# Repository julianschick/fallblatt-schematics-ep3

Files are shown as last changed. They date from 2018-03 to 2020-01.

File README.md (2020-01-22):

# Fallblattanzeiger der Deutschen Bahn

Die Deutsche Bahn verwendete lange Zeit standardisierte Fallblattanzeigemodule mit Platinen, die mit *MANTronic* beschriftet sind, also vermutlich von der Firma MAN hergestellt wurden.

Möchte man diese alten Module wieder zum klappern bringen, so hat man grundsätzlich erstmal zwei Möglichkeiten. Die Module wurden offenbar über eine RS485-Schnittstelle angesteuert. Das Protokoll ist vermutlich ein Protokoll ähnlich dem CAN-Bus. Meine gründliche Recherche ergab allerdings keine Quellen im Internet, denen bekannt ist, wie dieses Protokoll genau aussieht. Diese Möglichkeit ist daher eher schwierig.

Eine andere Möglichkeit besteht darin, den zentralen ZiLOG-Microcontroller auf der Platine durch einen eigenen Microcontroller zu ersetzen. Ich habe zu diesem Zweck den ZiLOG-Chip von der Platine geschnitten. Praktischerweise sind auf der Platine nicht nur die SMD-Lötpads für den ZiLOG-Chip, sondern auch etwas größere Pads im DIP-Raster, an die man sehr gut Kabel anlöten kann. Vermutlich ein überbleibsel von älteren Platinenversionen, bei denen ein größerer Microcontroller verwendet wurde.

Mit einer Kombination aus eigener Intuition und Bestätigung durch die Schaltpläne dieses [Hackaday-Projekts](https://hackaday.io/project/9070-fallblattfahrzielanzeige-of-s-bahn-berlin) war es nicht schwer, die Pinbelegung des ZiLOG-Controllers zu ermitteln und so herauszufinden, welche Pins angesteuert bzw. ausgelesen werden müssen. Weiter unten habe ich das mit einer Skizze und einem Foto dokumentiert.

Gemäß der Einteilung im [Wikipedia-Artikel](https://de.wikipedia.org/wiki/Fallblattanzeige) in die vom Aufbau her zu unterscheidenden Epochen 1 bis 4 fällt diese Anzeige in die Epoche 3.

## Funktionsweise

Die Funktionsweise des Fallblattmoduls ist gar nicht so kompliziert. Die Blätter sitzen auf einer Welle die über ein Getriebe von einem Synchronmotor (Berger Lahr RSM 42/12 NG) angetrieben wird, der tatsächlich auch heute noch erhältlich ist ([Datenblatt](https://www.abi.nl/assets/uploads/Downloads/Aandrijvingen/Kleine%20vertragingsmotoren/Synchroonmotoren/Catalogus_RSM_D.pdf)).
Damit der Motor weiß, wann er anhalten soll, sind zwei Infrarot-Transmitter mit Photodioden als Sensoren verbaut. Ein Sensor erzeugt pro fallendem Blatt einen erhöhten Spannungspegel, der andere dient zur Erkennung der Nullposition und weist nur einmal pro Umdrehung der ganzen Welle einen erhöhten Spannungspegel auf. Das ganze wird durch weiße Blenden bewerkstelligt, die beim Vorbeistreichen am Sensor durch die Reflektion der Infrarotstrahlen des Transmitters für mehr Einfall von Infrarotstrahlung in die Photodiode und dadurch einen höheren Spannungspegel sorgen.

Die Verdrahtung der Sensoren auf der Platine ist etwas eigenwillig. Beide Sensoren gehen auf den gleichen Eingang (Sensor IN), an dem mit Hilfe eines ADC die anliegende Spannung messen kann. Um die Sensoren einzeln abfragen zu können, kann man die Sensoren getrennt mit Spannung versorgen (Sensor 1 / Sensor 2) und dann jeweils nur den Sensor auslesen, der mit Spannung versorgt wird. Der Motor ist einfach anzusteuern: Zieht man den Motor-Pin auf LOW, läuft der Motor los, zieht man ihn auf HIGH (3,3V oder 5V), bleibt der Motor stehen.

## Pinbelegung ZiLOG
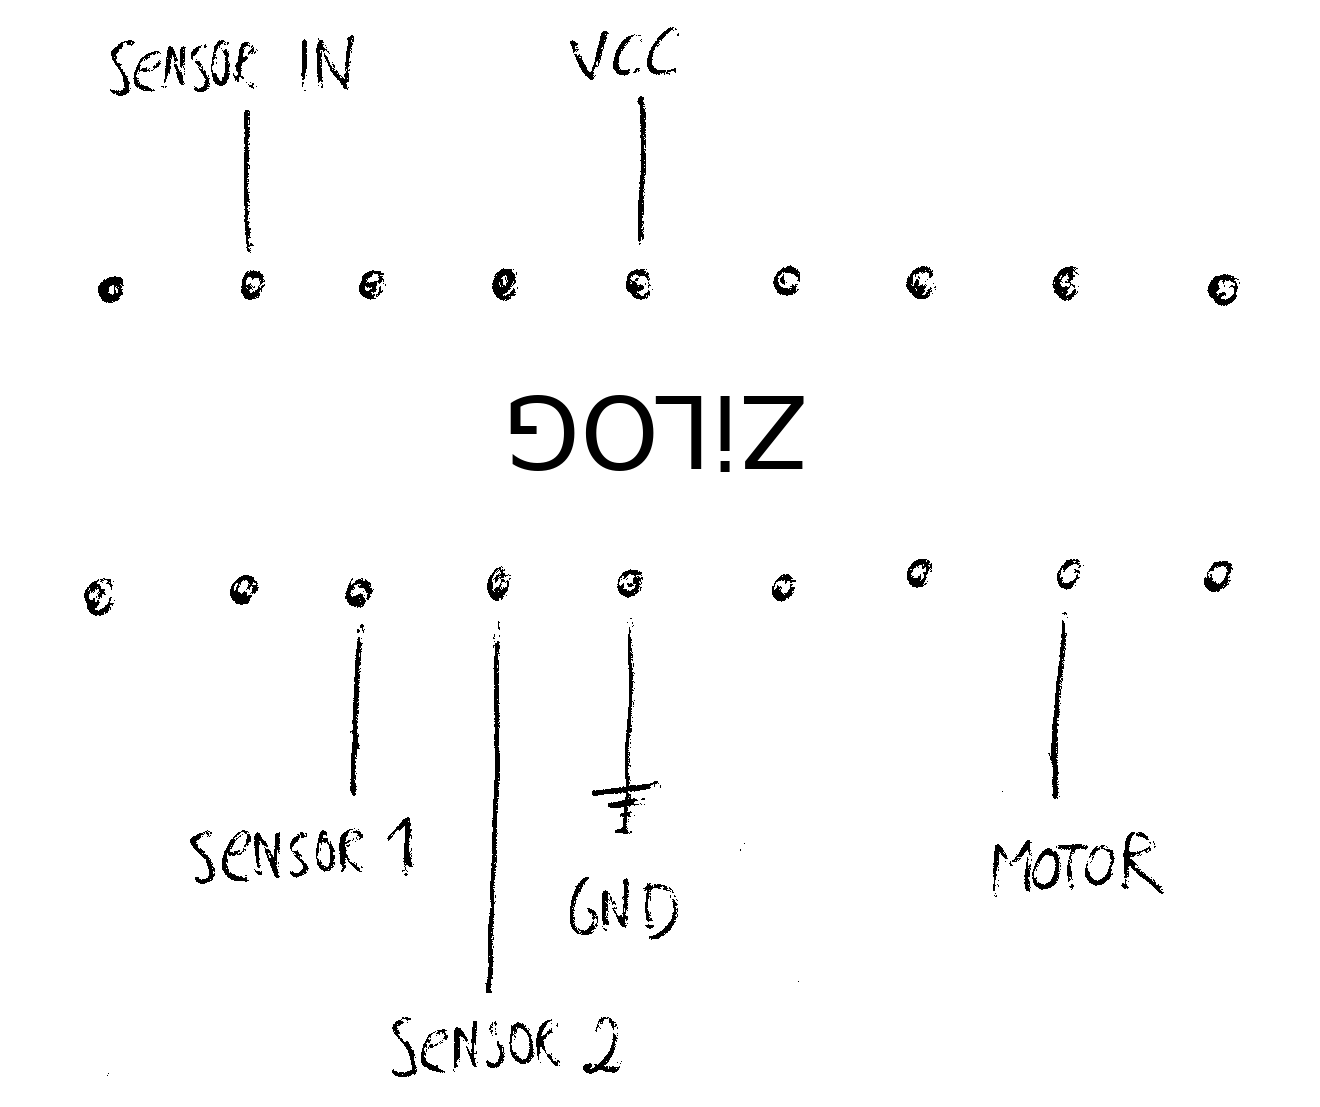
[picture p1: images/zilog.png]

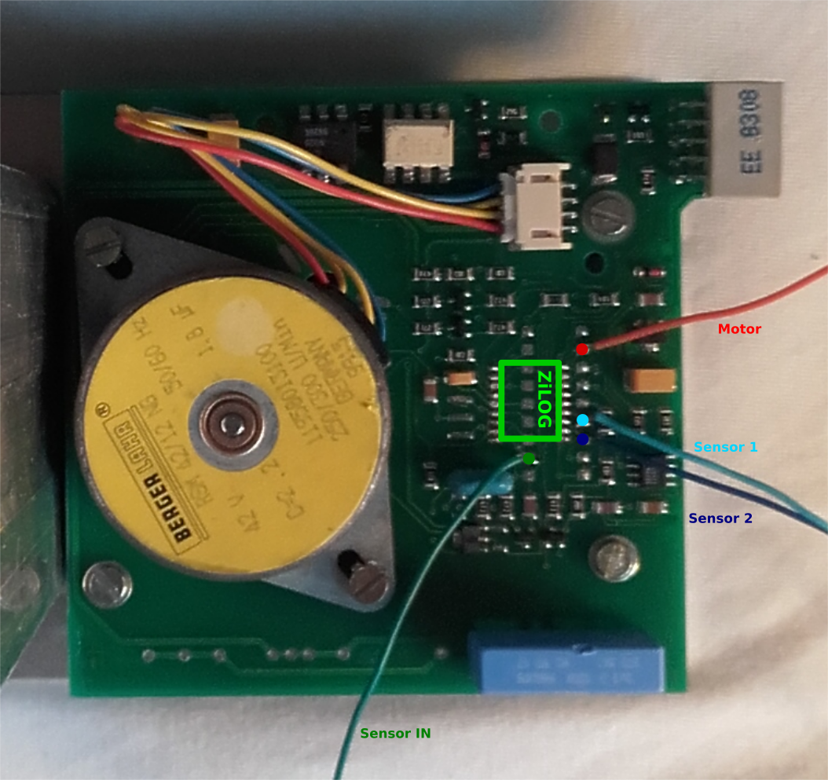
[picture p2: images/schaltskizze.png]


## Stromversorgung

Die Platine hat zwei Stromkreise, ein Niederspannungsstromkreis für die Steuerungselektronik, der ursprünglich wohl mit 5 V DC betrieben wurde. Ich habe auch mit nur 3.3 V DC keine Probleme festgestellt. Der andere Stromkreis sollte mit etwa 42 V AC bei 50 Hz gespeist werden. Mit diesem Strom wird der Synchronmotor zum Antrieb der Welle betrieben. Die folgende Skizze zeigt die Pinbelegung des Wannensteckers am Rand der Platine bezüglich der Spannungsversorgung.

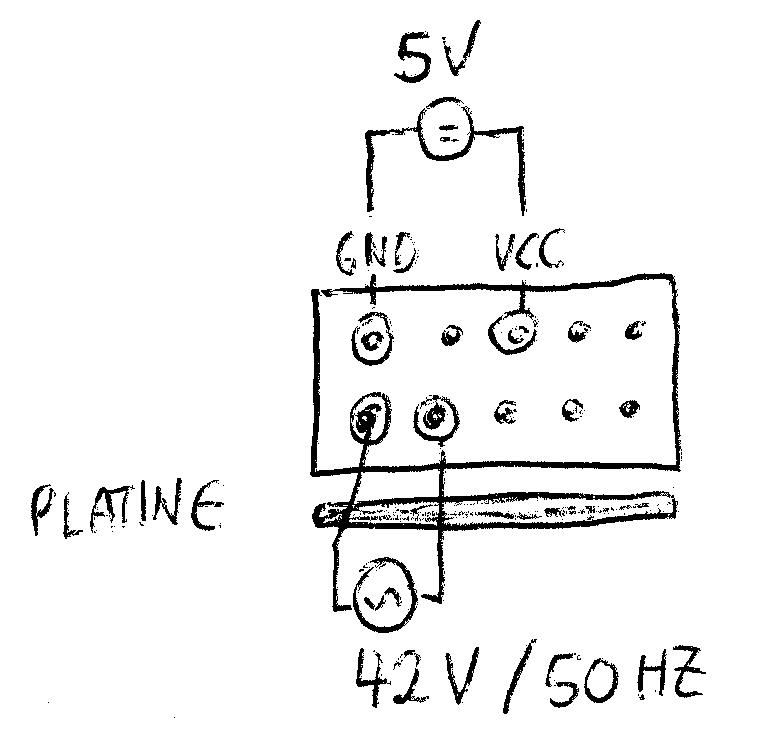
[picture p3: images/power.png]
Stromversorgung


## Code

Code für die Platine kann in den Repositories [fallblatt-code-legacy](https://github.com/julianschick/fallblatt-code-legacy) und [fallblatt-code](https://github.com/julianschick/fallblatt-code) gefunden werden, wobei letzterer aktueller und mit mehr Funktionen ausgestattet ist.

## Teileliste

Mit passenden Artikelbezeichnungen für den Berliner Elektroteilehändler [Segor](https://www.segor.de).

Anzahl | Beschreibung | Segor-Artikelbezeichnung | Alt. Link
--|--|--|--
1 | Schraubklemme 2-polig RM 7,5mm | *ARK 2-Lift/RM7,5*
1 | Varistor >300V RM 7,5mm | *VDR 300-K 7* | [Reichelt](https://www.reichelt.de/varistor-rm-7-5-mm-300-v-10-epc-b72210-s030-p239932.html)
1 | Brückengleichrichter Rund, Wechselstrompins gegenüber, RM 5mm | *B 80C1500 R* | [Reichelt](https://www.reichelt.de/brueckengleichrichter-100-v-1-5-a-b70c1500rund-p181713.html)
1 | Transformator 9V _Block VB 2,0/1/9_ | | [Reichelt](https://www.reichelt.de/printtrafo-2-va-9-v-222-ma-rm-20-mm-ei-30-15-5-109-p27328.html)
1 | Transformator 2x24V *Block VC 10/2/24* | | [Reichelt](https://www.reichelt.de/printtrafo-10-va-2x-24-v-2x-208-ma-rm-27-5-mm-ei-48-16-8-224-p27492.html)
1 | ESP32-Development-Board (es gibt 2 Varianten bei eBay, für diese Platine wird die unüblichere mit 19 Pins je Reihe und GND/VCC auf gegenüberliegenden, nicht nebeneinanderliegenden Pins benötigt; diese wird oft unter dem Namen _ESP32S_ verkauft.) |
1 | Spannungsregler 3,3V Formfaktor TO-220 _STM LD1117 V33C_ | *LD 1117 V33* | [Reichelt](https://www.reichelt.de/ldo-regler-fest-3-3-v-to-220-ld1117-v33c-p200891.html)
1 | Elektrolytkondensator 470u, >12V, RM 5mm | *ELRA 470u-25/105°lowESR* |
1 | Elektrolytkondensator 10u, >12V, RM 2mm | *ELRA 470u-35/105°* |
1 | Kondensator 100n, >12V, RM 2,5mm | *u10-R2.5-X7R* |
1 | D-Sub Buchse 9-polig, Printmontage 90°, Abstand Pinreihe zu Steckerfläche 10mm | DS09F-90°-10mm |
1 | D-Sub Buchse 25-polig, Printmontage 90°, Abstand Pinreihe zu Steckerfläche 10mm | DS25F-90°-10mm |
4 | Pinheader 20-polig, Female, Vertikal, RM 2,54mm | 
2 | Pinheader 2-polig, Male, Vertikal, RM 2,54mm

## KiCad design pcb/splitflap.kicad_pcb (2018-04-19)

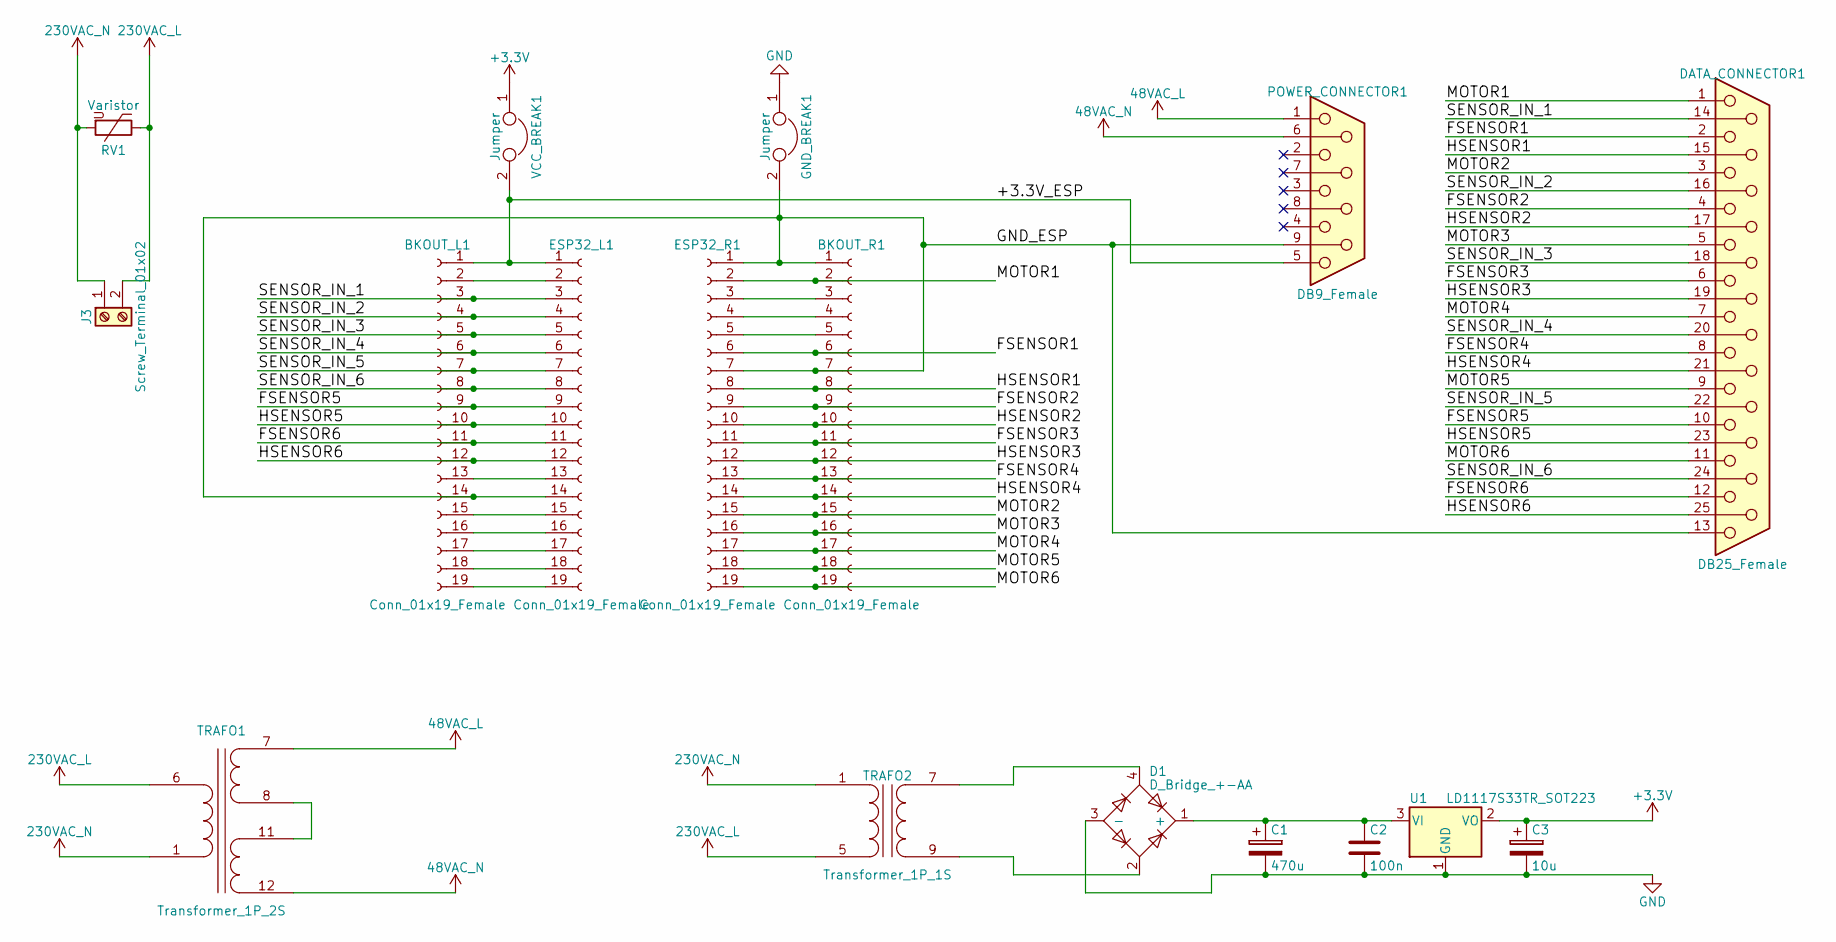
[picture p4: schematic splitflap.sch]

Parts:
BKOUT_L1: Conn_01x19_Female; Socket_Strip_Straight_1x20_Pitch2.54mm
BKOUT_R1: Conn_01x19_Female; Socket_Strip_Straight_1x20_Pitch2.54mm
C1: 470u; CP_Radial_D8.0mm_P5.00mm
C2: 100n; C_Rect_L4.0mm_W2.5mm_P2.50mm
C3: 10u; CP_Radial_D4.0mm_P2.00mm
D1: D_Bridge_+-AA; Diode_Bridge_Round_D8.9mm
DATA_CONNECTOR1: DB25_Female; DSUB-25_Female_Horizontal_Pitch2.77x2.54mm_EdgePinOffset9.4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
ESP32_L1, ESP32_R1: Conn_01x19_Female; Socket_Strip_Straight_1x20_Pitch2.54mm
GND_BREAK1: Jumper; Pin_Header_Straight_1x02_Pitch2.54mm
J3: Screw_Terminal_01x02; TerminalBlock_MetzConnect_Type171_RT13702HBWC_Pitch7.50mm
POWER_CONNECTOR1: DB9_Female; DSUB-9_Female_Horizontal_Pitch2.77x2.54mm_EdgePinOffset9.40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
RV1: Varistor; RV_Disc_D12_W3.9_P7.5
TRAFO1: Transformer_1P_2S; Transformer_CHK_EI48-10VA_2xSec_BLOCK
TRAFO2: Transformer_1P_1S; Transformer_CHK_EI30-2VA_1xSec
U1: LD1117S33TR_SOT223; TO-220-3_Vertical
VCC_BREAK1: Jumper; Pin_Header_Straight_1x02_Pitch2.54mm

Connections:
48VAC_L: POWER_CONNECTOR1.1, TRAFO1.7 (SA)
48VAC_N: POWER_CONNECTOR1.6, TRAFO1.12 (SD)
230VAC_L: J3.2, RV1.1, TRAFO1.6 (AA), TRAFO2.5 (AB)
230VAC_N: J3.1, RV1.2, TRAFO1.1 (AB), TRAFO2.1 (AA)
+3V3: C3.1, U1.2 (VO), VCC_BREAK1.1
/+3.3V_ESP: BKOUT_L1.1, ESP32_L1.1, POWER_CONNECTOR1.5, VCC_BREAK1.2
/FSENSOR1: BKOUT_R1.6, DATA_CONNECTOR1.2, ESP32_R1.6
/FSENSOR2: BKOUT_R1.9, DATA_CONNECTOR1.4, ESP32_R1.9
/FSENSOR3: BKOUT_R1.11, DATA_CONNECTOR1.6, ESP32_R1.11
/FSENSOR4: BKOUT_R1.13, DATA_CONNECTOR1.8, ESP32_R1.13
/FSENSOR5: BKOUT_L1.9, DATA_CONNECTOR1.10, ESP32_L1.9
/FSENSOR6: BKOUT_L1.11, DATA_CONNECTOR1.12, ESP32_L1.11
/GND_ESP: BKOUT_L1.14, BKOUT_R1.1, BKOUT_R1.7, DATA_CONNECTOR1.13, ESP32_L1.14, ESP32_R1.1, ESP32_R1.7, GND_BREAK1.2, POWER_CONNECTOR1.9
/HSENSOR1: BKOUT_R1.8, DATA_CONNECTOR1.15, ESP32_R1.8
/HSENSOR2: BKOUT_R1.10, DATA_CONNECTOR1.17, ESP32_R1.10
/HSENSOR3: BKOUT_R1.12, DATA_CONNECTOR1.19, ESP32_R1.12
/HSENSOR4: BKOUT_R1.14, DATA_CONNECTOR1.21, ESP32_R1.14
/HSENSOR5: BKOUT_L1.10, DATA_CONNECTOR1.23, ESP32_L1.10
/HSENSOR6: BKOUT_L1.12, DATA_CONNECTOR1.25, ESP32_L1.12
/MOTOR1: BKOUT_R1.2, DATA_CONNECTOR1.1, ESP32_R1.2
/MOTOR2: BKOUT_R1.15, DATA_CONNECTOR1.3, ESP32_R1.15
/MOTOR3: BKOUT_R1.16, DATA_CONNECTOR1.5, ESP32_R1.16
/MOTOR4: BKOUT_R1.17, DATA_CONNECTOR1.7, ESP32_R1.17
/MOTOR5: BKOUT_R1.18, DATA_CONNECTOR1.9, ESP32_R1.18
/MOTOR6: BKOUT_R1.19, DATA_CONNECTOR1.11, ESP32_R1.19
/SENSOR_IN_1: BKOUT_L1.3, DATA_CONNECTOR1.14, ESP32_L1.3
/SENSOR_IN_2: BKOUT_L1.4, DATA_CONNECTOR1.16, ESP32_L1.4
/SENSOR_IN_3: BKOUT_L1.5, DATA_CONNECTOR1.18, ESP32_L1.5
/SENSOR_IN_4: BKOUT_L1.6, DATA_CONNECTOR1.20, ESP32_L1.6
/SENSOR_IN_5: BKOUT_L1.7, DATA_CONNECTOR1.22, ESP32_L1.7
/SENSOR_IN_6: BKOUT_L1.8, DATA_CONNECTOR1.24, ESP32_L1.8
GND: C1.2, C2.2, C3.2, D1.3 (-), GND_BREAK1.1, U1.1 (GND)
unnamed: BKOUT_L1.2, ESP32_L1.2
unnamed: BKOUT_L1.13, ESP32_L1.13
unnamed: BKOUT_L1.15, ESP32_L1.15
unnamed: BKOUT_L1.16, ESP32_L1.16
unnamed: BKOUT_L1.17, ESP32_L1.17
unnamed: BKOUT_L1.18, ESP32_L1.18
unnamed: BKOUT_L1.19, ESP32_L1.19
unnamed: BKOUT_R1.3, ESP32_R1.3
unnamed: BKOUT_R1.4, ESP32_R1.4
unnamed: BKOUT_R1.5, ESP32_R1.5
unnamed: C1.1, C2.1, D1.1 (+), U1.3 (VI)
unnamed: D1.2, TRAFO2.9 (SA)
unnamed: D1.4, TRAFO2.7 (SB)
unnamed: TRAFO1.8 (SB), TRAFO1.11 (SC)

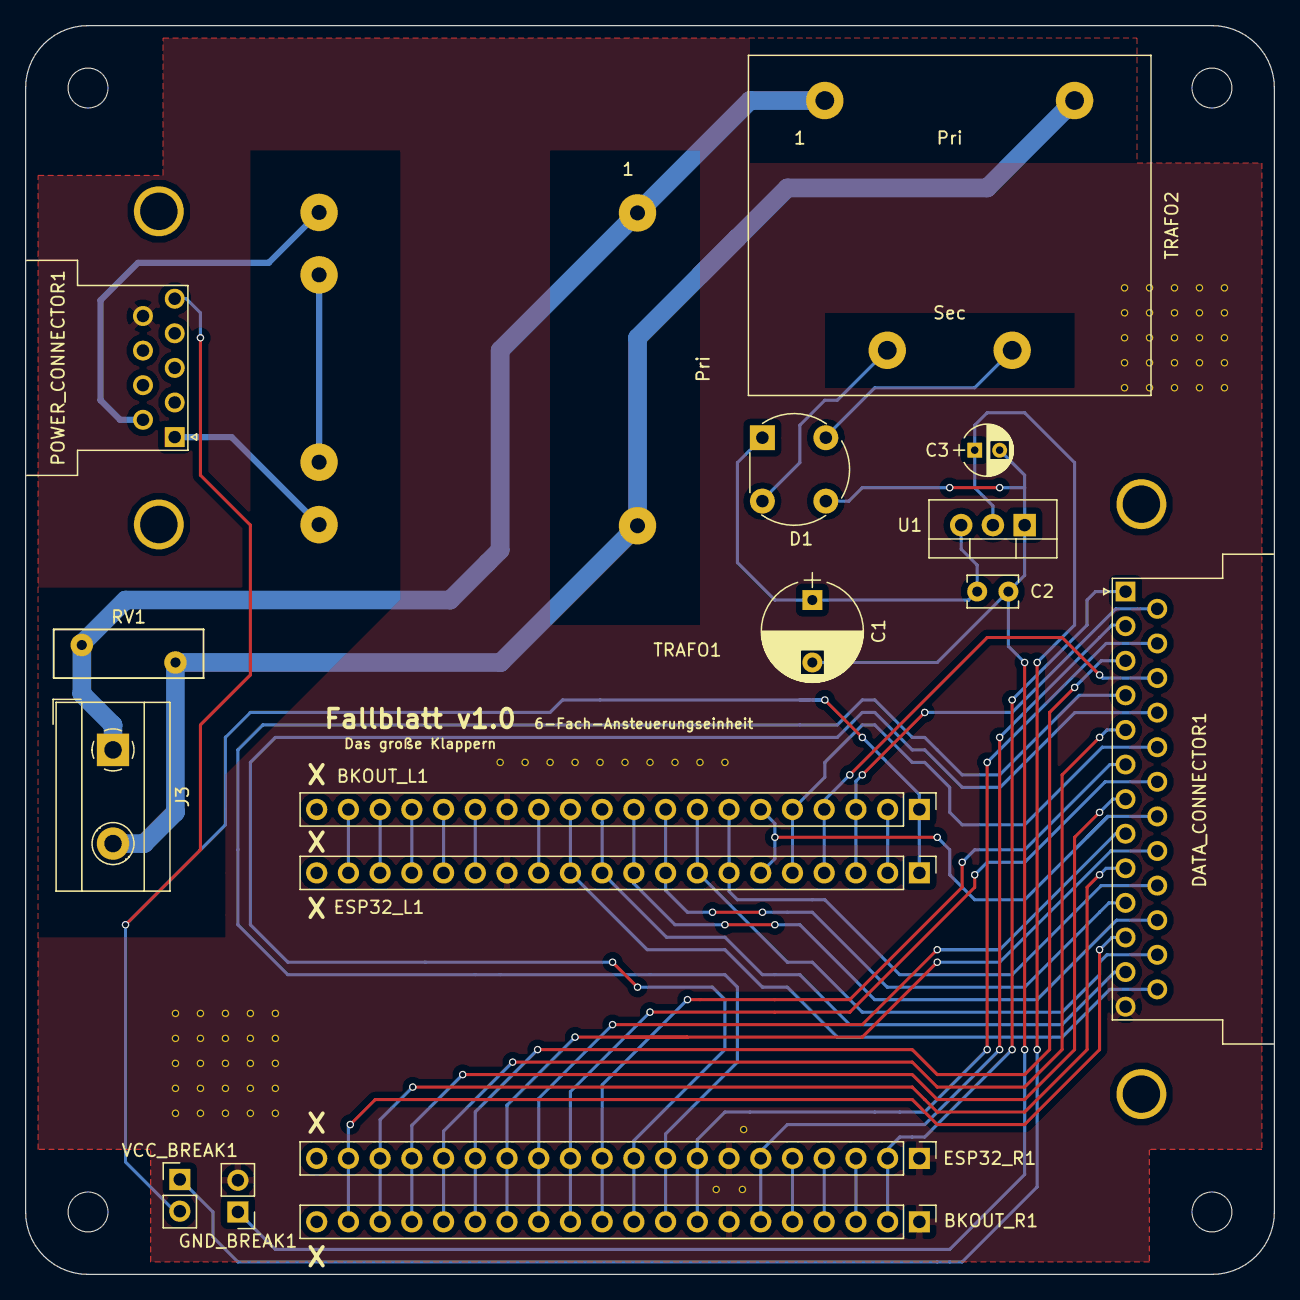
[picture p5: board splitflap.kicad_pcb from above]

Board: 2 copper layers, 100.0 x 100.0 mm, 17 parts (0 on the bottom side), 46 nets.

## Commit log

2018-03-30 platine v1
    [splitflap.kicad_pcb, splitflap.sch]
2018-04-16 fix vias
    [splitflap.kicad_pcb]
2018-04-16 net width trafo1 wrong
    [splitflap.kicad_pcb]
2018-04-19 gerber files
    [splitflap-B.Cu.gbl, splitflap-B.Mask.gbs, splitflap-Edge.Cuts.gm1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]
2018-05-09 bugfixes / extension bt interface
    [partitions.csv]
2018-05-16 bugfixes / getip
    [partitions.csv]
2019-01-22 special symbols moved
    [splitflap.sch]
2019-10-24 moved code away
    [partitions.csv]
